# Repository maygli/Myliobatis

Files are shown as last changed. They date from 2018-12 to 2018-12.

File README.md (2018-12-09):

# Myliobatis
FDM 3D printer motherbords based on STM32F407VG/STM32F103RE
This projects contains design of motherbords for FDM 3d printers. Where 3 variants of its:
1) <b>Mobula Ray</b>. This motherbords based on STM32F407VG microcontroller. Motherbords contains:
  - 6 stepper motors drivers TMC2224 (same as TMC2208) controlled by UART. Microsteps, stepper are current controlled by firmware. 
  - 6 PWM output - Heatbed, 3 x heaters, 2 controlled fans
  - 4 temperature inputs
  - 6 inputs for XMIN, XMAX, YMIN, YMAX, ZMIN, ZMAX
  - 3 inputs for filament detectors
  - BlTouch connector
  - onboard WiFi
  - connector for external GSM module
  - connectors SPI/I2C/UART interfaces
  - EXT1/EXT2 connectrs for displays/external SD card
  - SWD connector
  - USB-B
  - micro SD
  - switch after end of print output
  - connectors for 9 programmable pins 
  - board size 150 x 120 mm
  <br>Project page on easyeda.com https://easyeda.com/mmaygli/mid-bro
  2) <b>Manta Ray</b>. This motherbords based on STM32F407VG microcontroller. Has two variants. Variant A has common power suplay for heaters/fans and drivers. 
  Variant B has separate connectors for heaters and motor drivers. Motherbords contains:
  - Connectrs for 6 stepper motors compatible with A4988 (A4988, DRV8825, TMC2100, TMC2130, TMC2208, etc). 
  - 6 PWM output - Heatbed, 3 x heaters, 2 controlled fans
  - 4 temperature inputs
  - 6 inputs for XMIN, XMAX, YMIN, YMAX, ZMIN, ZMAX
  - 3 inputs for filament detectors
  - BlTouch connector
  - onboard WiFi
  - connector for external GSM module
  - connectors SPI/I2C/UART interfaces
  - EXT1/EXT2 connectrs for displays/external SD card
  - SWD connector
  - USB-B
  - micro SD
  - switch after end of print output
  - connectors for 13 programmable pins
  - board size 150 x 120 mm
  <br>Project pages on easyeda.com: https://easyeda.com/mmaygli/test3d, https://easyeda.com/mmaygli/bigbro-external-drivers-common-power
  1) <b>Sting Ray</b>. This motherbords based on STM32F103RE microcontroller.  
  Variant B has separate connectors for heaters and motor drivers. Motherbords contains:
  - Connectrs for 5 stepper motors compatible with A4988 (A4988, DRV8825, TMC2100, TMC2130, TMC2208, etc). 
  - 4 PWM output - Heatbed, 2 x heaters, 1 controlled fans
  - 3 temperature inputs
  - 6 inputs for XMIN, XMAX, YMIN, YMAX, ZMIN, ZMAX
  - filament detector input
  - BlTouch connector (shared with ZMAX, YMAX)
  - connectors I2C/UART interfaces
  - EXT1/EXT2 connectrs for displays/external SD card
  - SWD connector
  - USB-B
  - micro SD
  - board size 112 x 100 mm
<br>Project page on easyeda.com https://easyeda.com/mmaygli/stm32f103-3d-printer-board
<br> Status on 9 of Dec 2018: <b>Boards just designed. Its have never be assembled and tested</b>

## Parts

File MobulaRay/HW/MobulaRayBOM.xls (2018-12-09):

ID | Name | Designator | Footprint | Quantity | Manufacturer Part
1 | TC4427AEOA713 | U1,U7,U8 | SOIC-8_150MIL | 3 | TC4427AEOA713
2 | Hotbead | LED1 | LED-0805 | 1 | 17-21/GHC-YR1S2/3T
3 | Extruder1 | LED2 | LED-0805 | 1 | 17-21/GHC-YR1S2/3T
4 | KF301-2P | EXTRUDER1,EXTRUDER2,EXTRUDER3 | KF301-2P | 3 | ?
5 | KF129-5.08 | HEATBED,POWER | KF129-5.08 | 2 | KF129-5.08
6 | 10 | R20,R7,R8,R18,R37,R13 | 0603' | 6 | 0603WAF1002T5E
7 | 100K | R4,R9,R10,R19,R38,R14 | 0603' | 6 | 0603WAF1002T5E
8 | 3.3K | R5,R6,R11,R24,R21,R36,R12 | 0603' | 7 | 0603WAF1002T5E
9 | IRL3803S | Q5,Q2,Q3,Q7,Q4,Q1 | TO-263-2-COLD | 6 | IRL3803S
10 | Extruder2 | LED3 | LED-0805 | 1 | 17-21/GHC-YR1S2/3T
11 | XH-2A black RHOS | FAN1,TBED1,TEXTR1,TEXTR2,FAN3,+5V,+3.3V,FAN2,TEXTR3 | XH-2A | 9 | XH-2A black RHOS
12 | 22 | R22,R15 | 0603' | 2 | 0603WAF1002T5E
13 | 1.5K | R25 | 0603' | 1 | 0603WAF1002T5E
14 | USB-B-Female-TH_C46393 | USB1 | USB-M-49 | 1 | USB-B-Female-90-TH
15 | Micro SD Card Holder; | J1 | MICRO-SD9+4P-SMD-16.1X14.5X1.85MM | 1 | ?
16 | 47K | R23,R26,R30,R31,R32 | 0603' | 5 | 0603WAF1002T5E
17 | LM2596R-5.0 | U9 | TO-263-5-COLD | 1 | LM2596R-5.0
18 | 100nF | C19,C28,C32,C33,C26,C30,C25,C39,C52,C53,C54,C55,C56,C57 | C0603 | 14 | CC0603KRX7R9BB104
19 | AMS1117-3.3 | U10 | SOT-223 | 1 | AMS1117-3.3
20 | 220uF | C31 | CAP-D6.3XH5.5 | 1 | UT1A221M0605VG
21 | 470uF | C34 | CAP-D12.5XH13.5 | 1 | RVT1V681M1213
22 | SS54 | D1 | SMB(DO-214AA) | 1 | SS54
23 | Power | LED5 | LED-0805 | 1 | 17-21/GHC-YR1S2/3T
24 | 100uF | C27 | CAP-D6.3XH5.5 | 1 | MV101M6R3E055A
25 | 10 uF | C20 | 0603' | 1 | 0603F105M160NT
26 | 10KΩ | R16,R17,R41,R33 | 0603' | 4 | 0603WAF1002T5E
27 | 1N4148W | D2 | SOD-123 | 1 | 1N4148W
28 | 49S8M | Y1 | HC49US | 1 | 49S8M
29 | 22pF | C21,C22 | C0603 | 2 | CC0603JRNPO9BN150
30 | 100uH | L1 | AXIAL-0.5 | 1 | LGA0410-102KP52E
31 | PADI | U25 | PADI(RTL8710) | 1 | pine64
32 | XH-3A | XMIN,YMIN,ZMIN,XMAX,YMAX,ZMAX,FILAMENT1,FILAMENT2,POWER_CONTROL,FILAMENT3 | XH-3A | 10 | XH-3A
33 | 3KΩ | R28,R34,R35,R29 | 0603' | 4 | RK73B1JTTD302J
34 | 10uF | C9,C18,C41,C23 | 0603' | 4 | CL10A106MO8NQNC
35 | FAN2 | LED6 | LED-0805 | 1 | 17-21/GHC-YR1S2/3T
36 | Header-Male-2.54_1x4 | I2C,UART,GSM,SPI | 210S-1X4P | 4 | 210S-1*4P L=11.6MMGold-plated black
37 | Header-Male-2.54_1x2 | BLTOUCH2,H2,H3,H5 | HDR-2X1/2.54 | 4 | 826629-2
38 | Header-Male-2.54_1x3 | BLTOUCH1 | HDR-3X1/2.54 | 1 | Header2.54mm 1*3P
39 | 4.7K | R39,R40 | 0603' | 2 | 0603WAF1002T5E
40 | Header-Male-2.54_1x5 | H1,H4 | DIP-1X5P-2.54MM-M | 2 | 210S-1*5P L=11.6MMGold-plated black
41 | IDC Box 2.0mm 2X5P | EXT2,EXT1 | HDR-IDC-2.0-2X5P | 2 | IDC Box 2.0mm 2X5P
42 | BC847A | Q8 | SOT23-3 | 1 | ?
43 | 47uH | L5 | SMD-10.0X10.0-10A50 | 1 | ABG10A50M470
44 | 7812T | U11 | TO220H | 1 | ?
45 | 100nF | C10,C16,C1,C2,C3,C7,C8,C35,C42,C43,C45,C49,C50,C59,C63,C64,C66,C70,C71,C73 | C0603 | 20 | 0603B104K500NT
46 | 100uF | C11,C29,C17,C24,C44,C58,C65,C72 | CAP-D6.3XH7.7 | 8 | UT1V101M0607VG
47 | LED | LED8 | LED-0805 | 1 | 17-21/GHC-YR1S2/3T
48 | FAN1 | LED4 | LED-0805 | 1 | 17-21/GHC-YR1S2/3T
49 | 1N4007 | D4 | 1N4007_SURFACE_MOUNT_M1_THRU_M7 | 1 | ?
50 | S3MB | D3 | SMB(DO-214AA) | 1 | S3MB
51 | BOOT0 | CN1 | H3-2.54 | 1 | ?
52 | Reset | SW3 | KEY-6.0*6.0 | 1 | Switch,6*6*5Plastic head,260G, 0.25mm,DIP2
53 | 74HC4051PW,118 | U14 | TSSOP-16 | 1 | 74HC4051PW,118
54 | TMC2224 | U2,U3,U4,U5,U6,U12 | QFN28G_0.5-5X5MM | 6 | TMC2224
55 | XH-4AK M | E3,E2,E1,X,Y,Z,Z1,Z2 | XH-4A | 8 | -
56 | 22nF | C4,C6,C37,C40,C46,C48,C60,C62,C67,C69,C74,C76 | C0603 | 12 | 0603B104K500NT
57 | 2.2uF | C5,C38,C47,C61,C68,C75 | C0603 | 6 | 0603B104K500NT
58 | 0.1Ω | R1,R2,R3,R42,R43,R44,R45,R46,R47,R48,R49,R50 | 2512 | 12 | 2512W4F100LT5E
59 | Header-Male-2.54_1x4 | EXT3_DRV,EXT2_DRV,X_DRV,Y_DRV,Z_DRV,EXT1_DRV | DIP-1X4P-2.54MM-M | 6 | 210S-1*4P L=11.6MMGold-plated black
60 | STM32F407VGT6 | U13 | LQFP-100_14X14X05P | 1 | STM32F407VGT6

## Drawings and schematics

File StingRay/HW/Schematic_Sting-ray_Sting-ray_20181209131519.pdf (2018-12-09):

# Vmot 16 Motor Connection

+5V

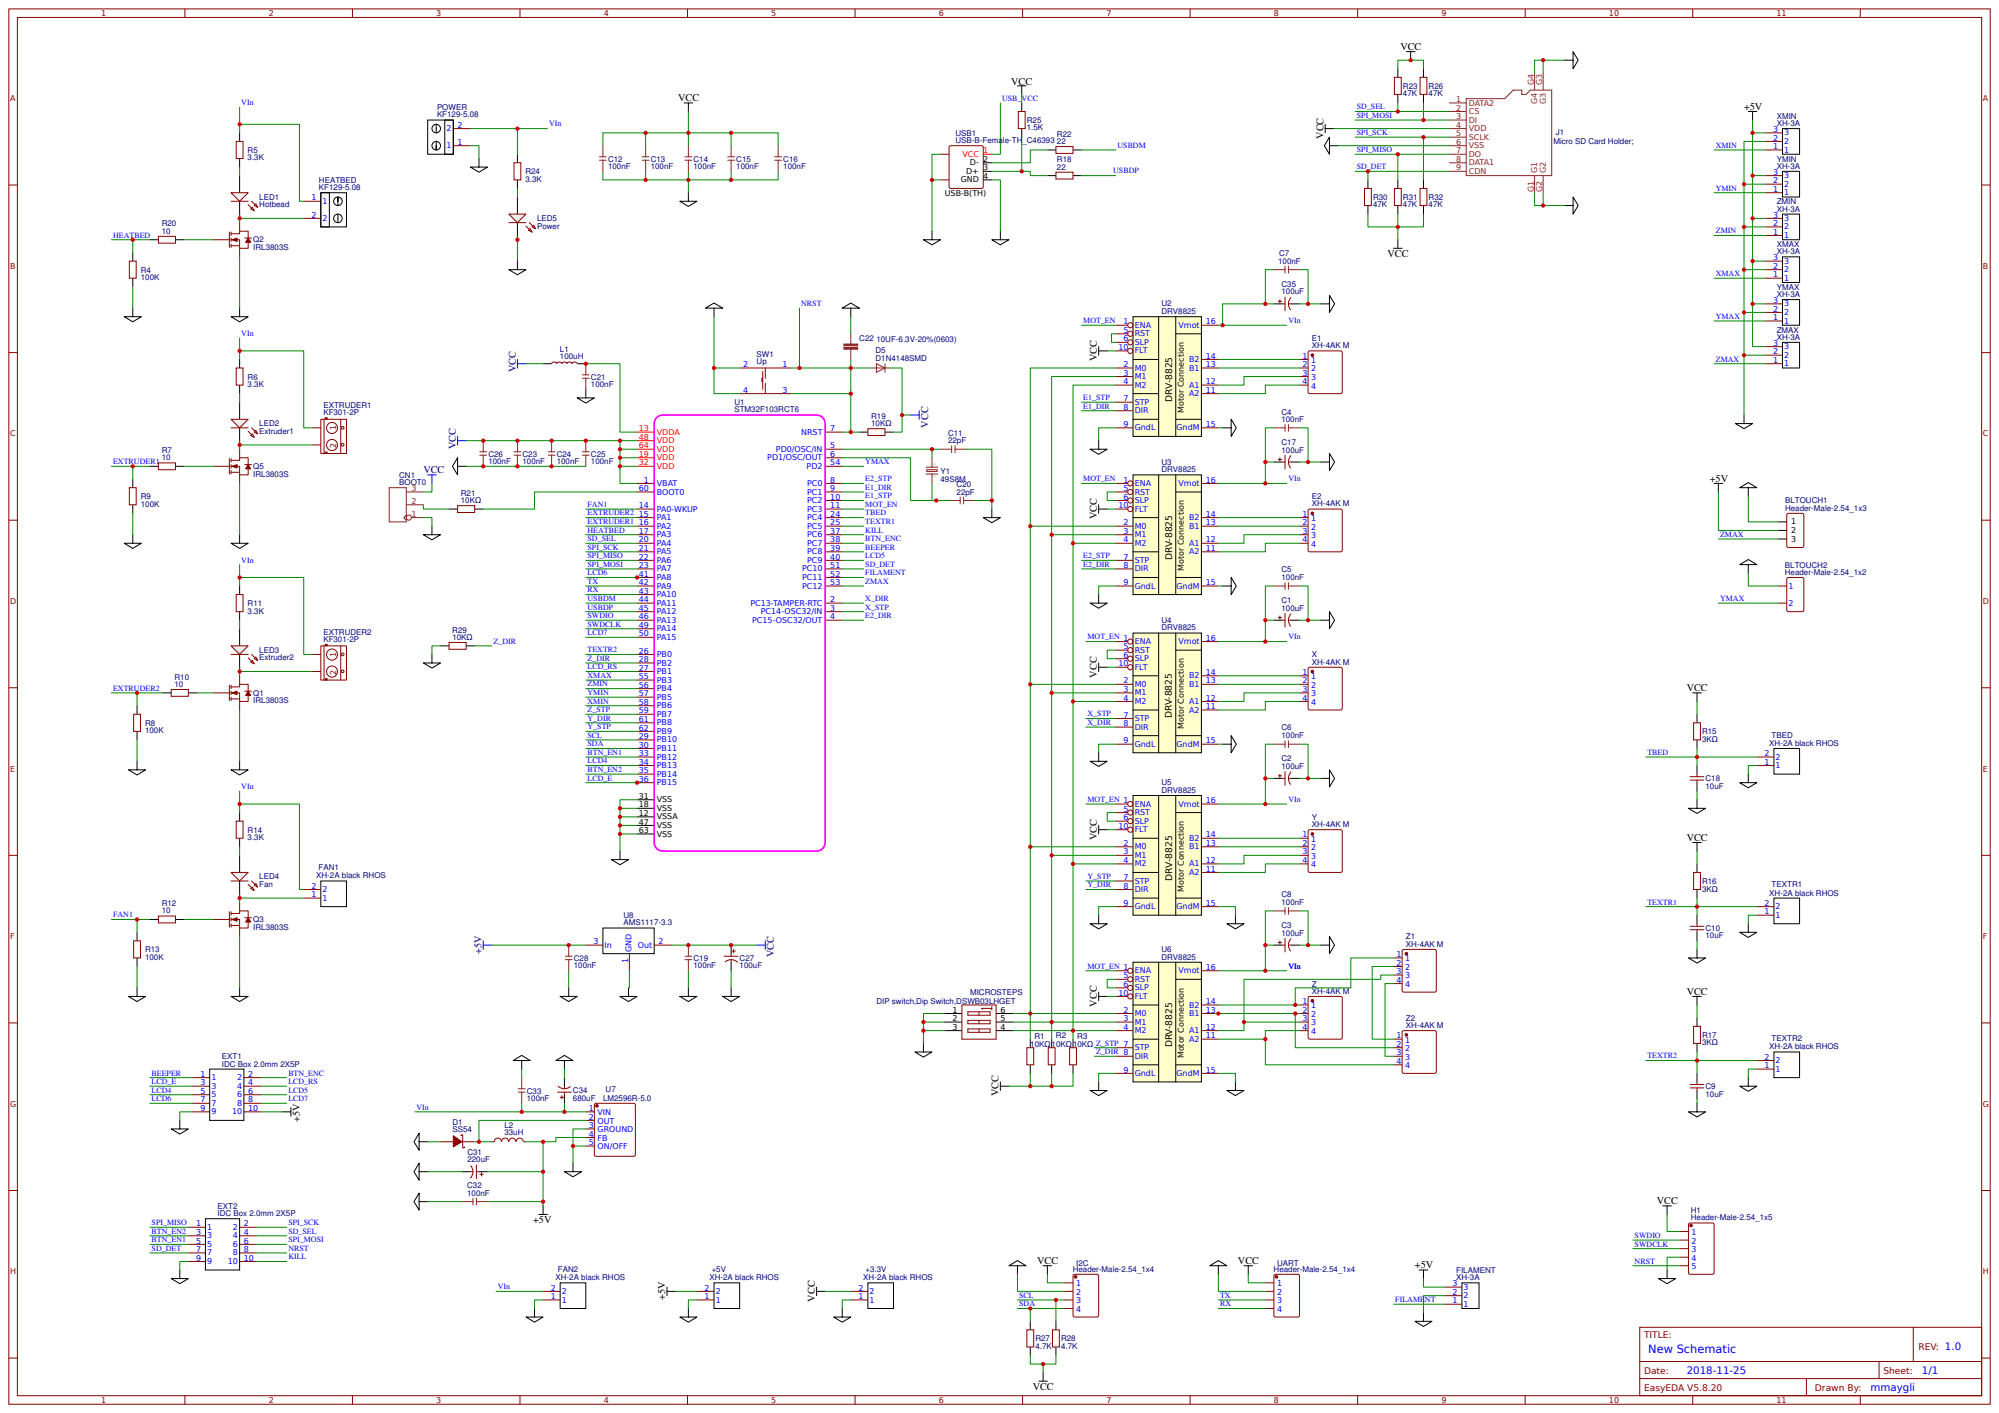
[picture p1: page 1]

Micro SD Card Holder;

DIP switch,Dip Switch,DSWB03LHGET

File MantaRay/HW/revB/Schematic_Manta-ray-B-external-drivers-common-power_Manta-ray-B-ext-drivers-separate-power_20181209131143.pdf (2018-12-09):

### VCC

### VCC

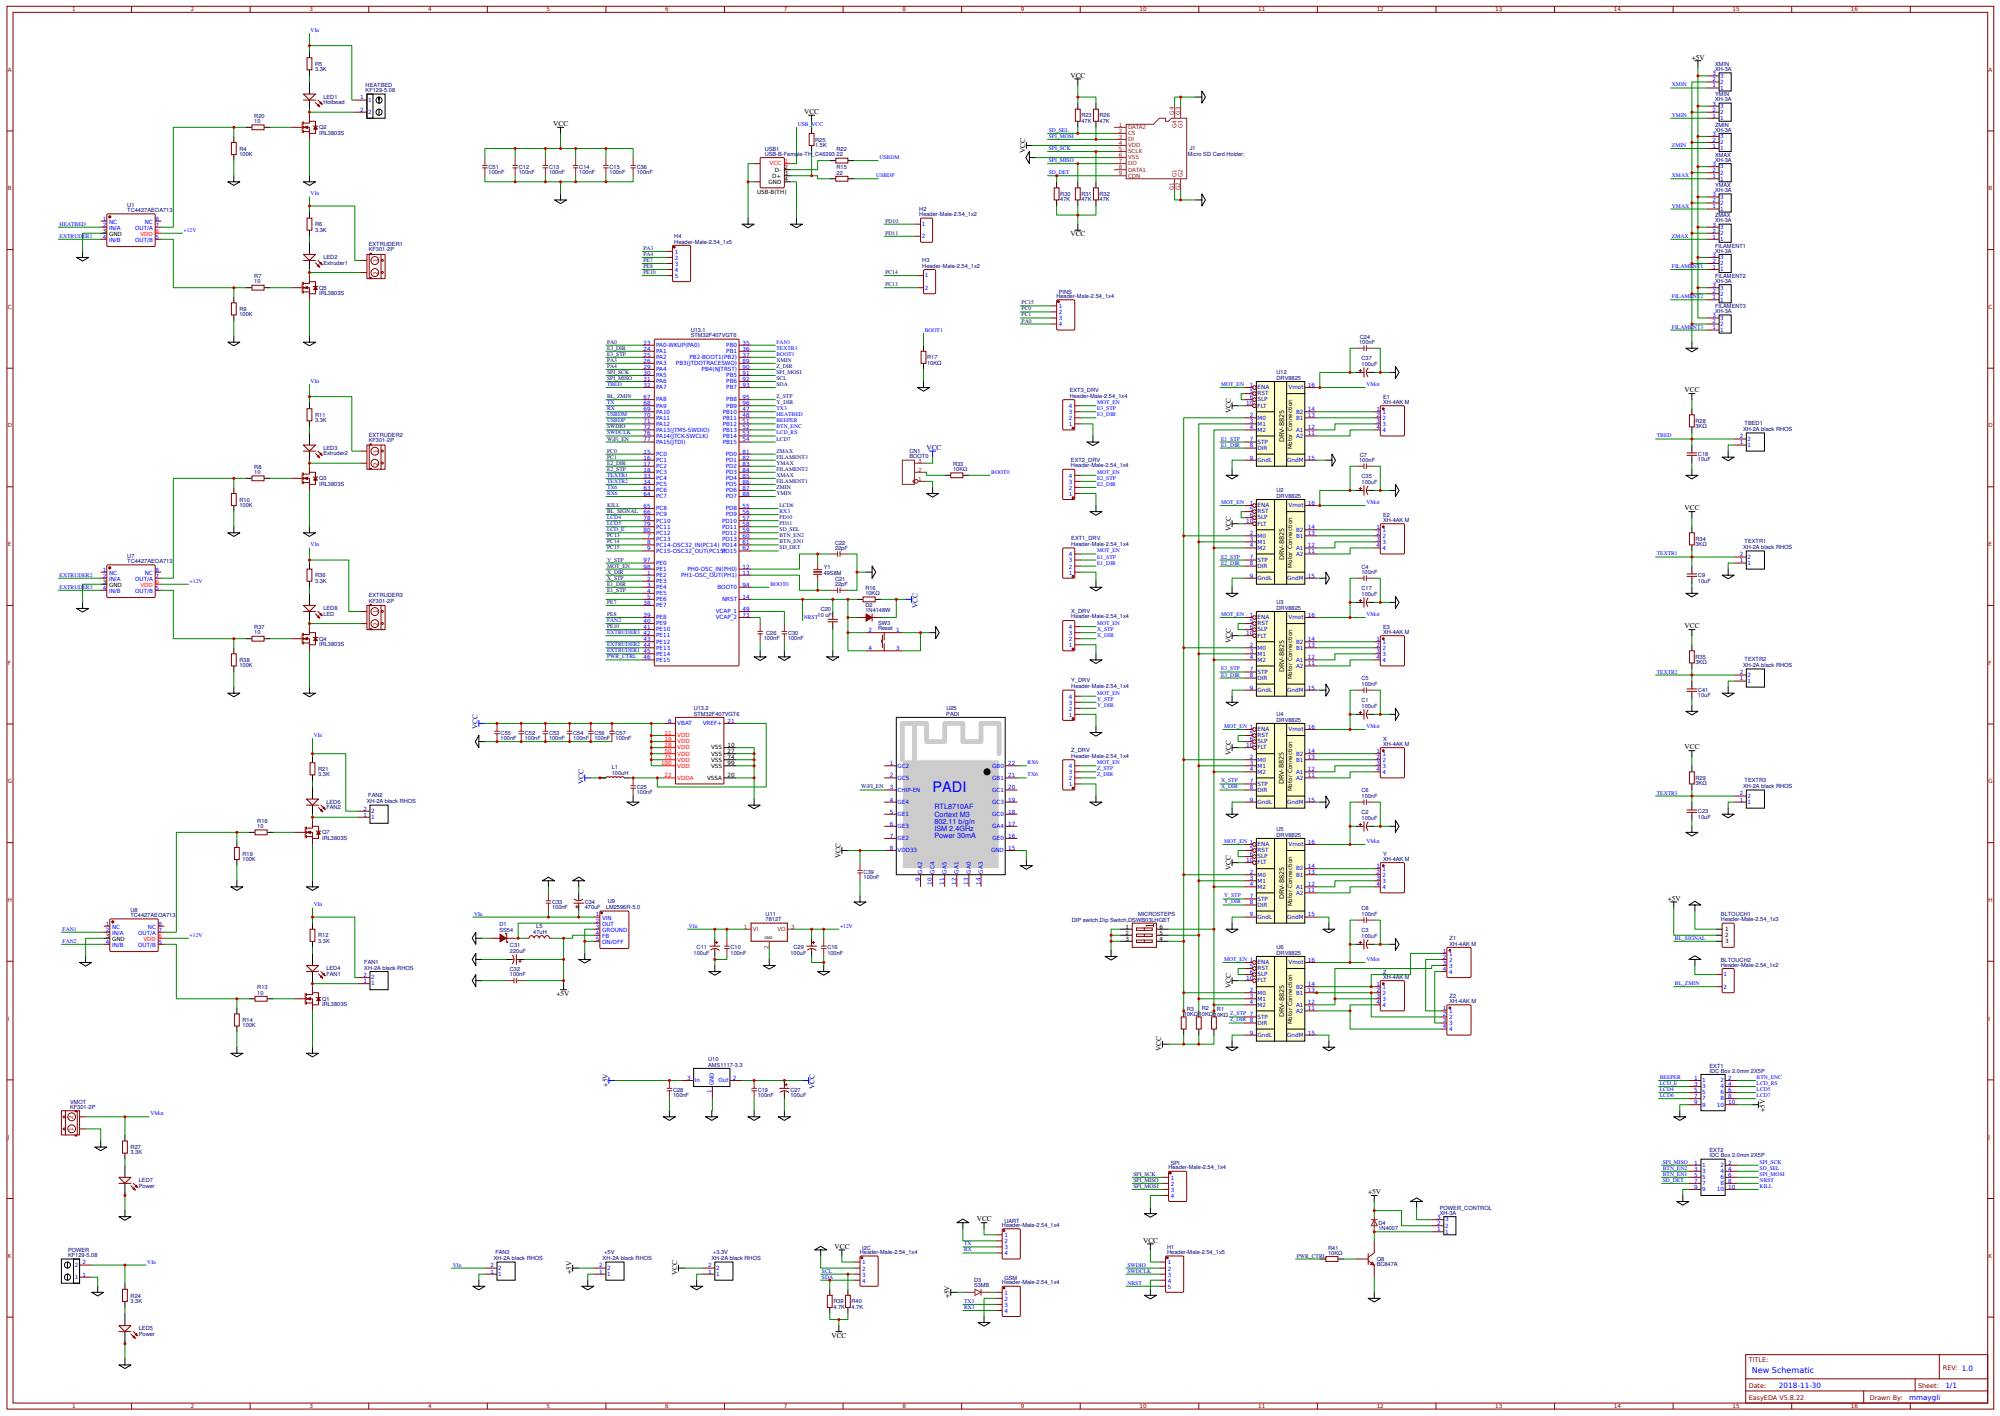
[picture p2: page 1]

Micro SD Card Holder;

DIP switch,Dip Switch,DSWB03LHGET

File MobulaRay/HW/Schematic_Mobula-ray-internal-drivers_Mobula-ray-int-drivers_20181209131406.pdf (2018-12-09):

### VCC

### VCC

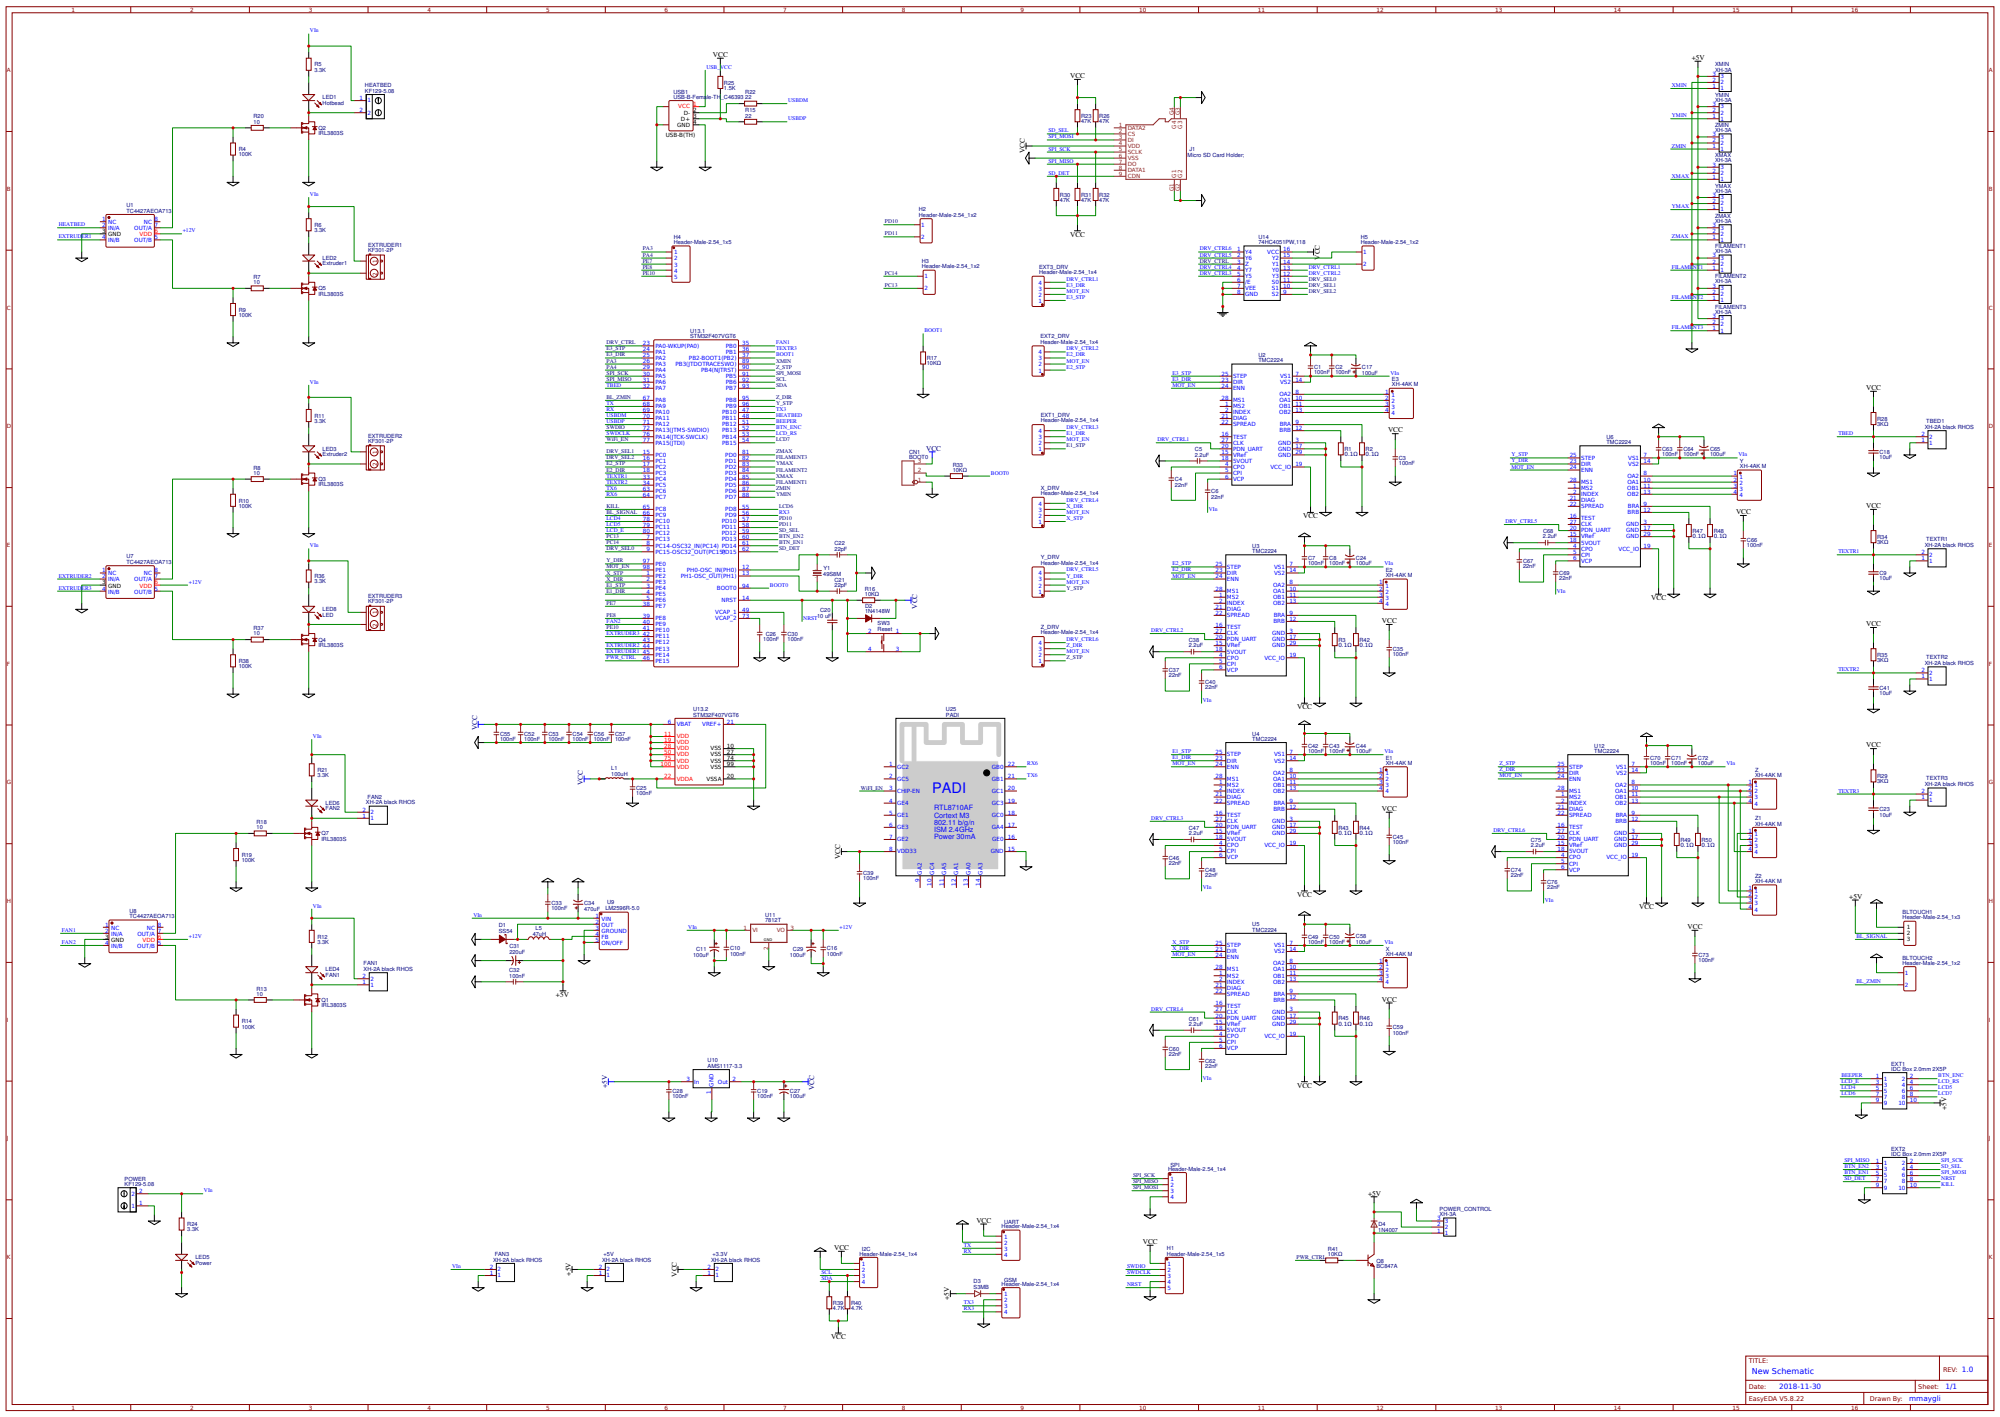
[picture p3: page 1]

Micro SD Card Holder;

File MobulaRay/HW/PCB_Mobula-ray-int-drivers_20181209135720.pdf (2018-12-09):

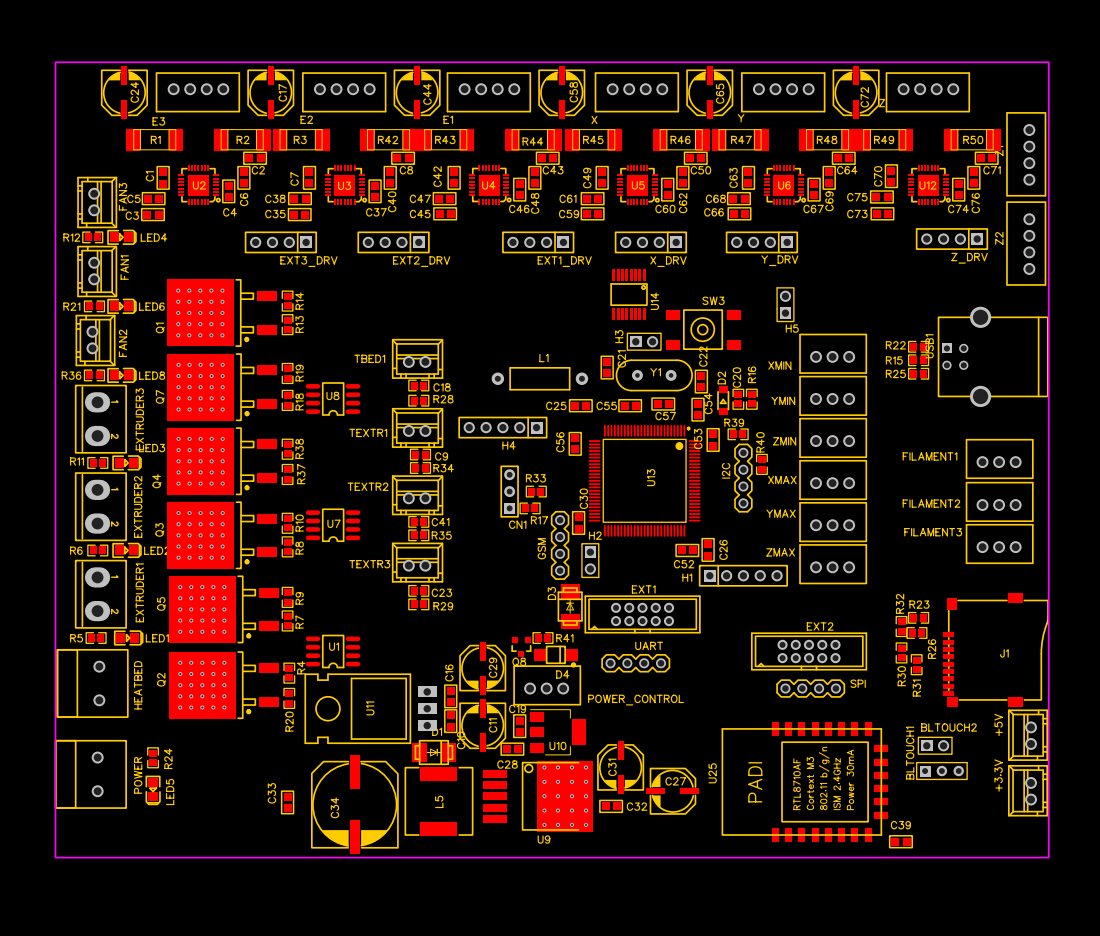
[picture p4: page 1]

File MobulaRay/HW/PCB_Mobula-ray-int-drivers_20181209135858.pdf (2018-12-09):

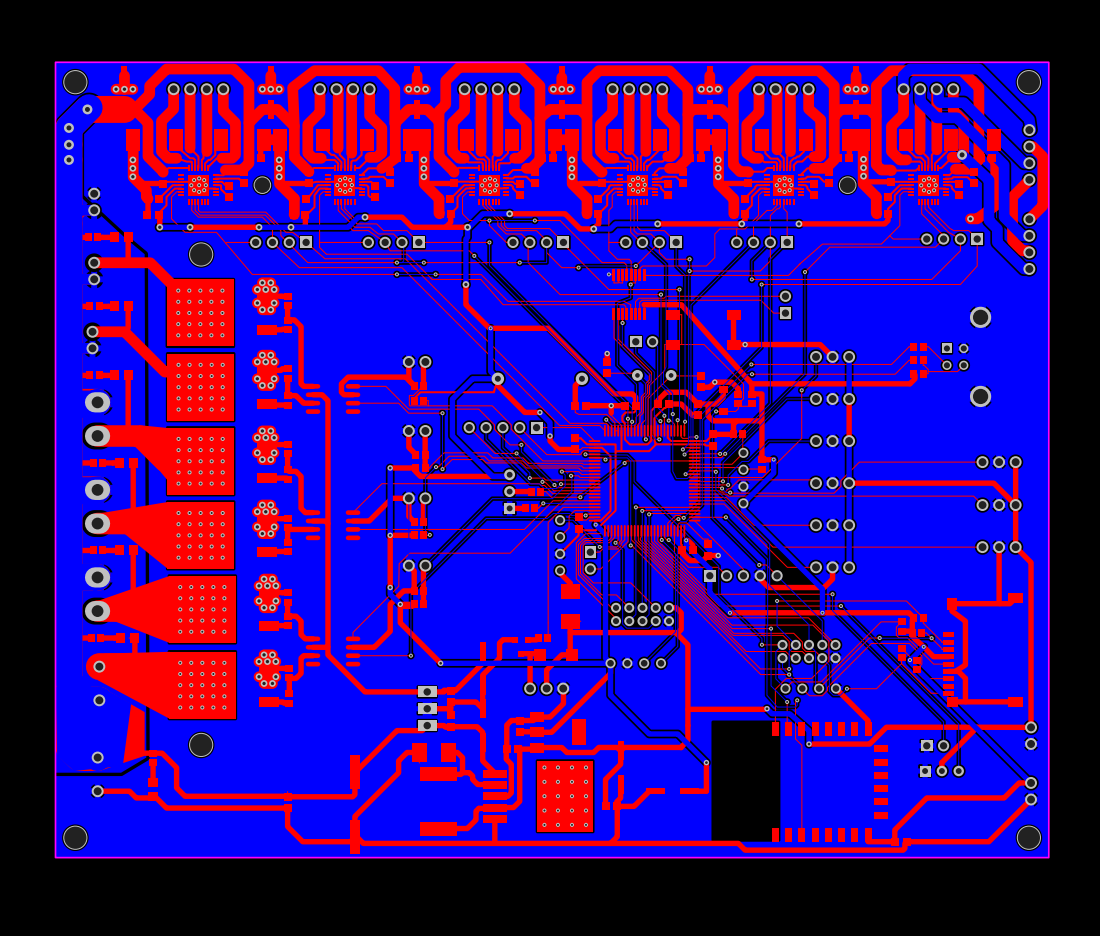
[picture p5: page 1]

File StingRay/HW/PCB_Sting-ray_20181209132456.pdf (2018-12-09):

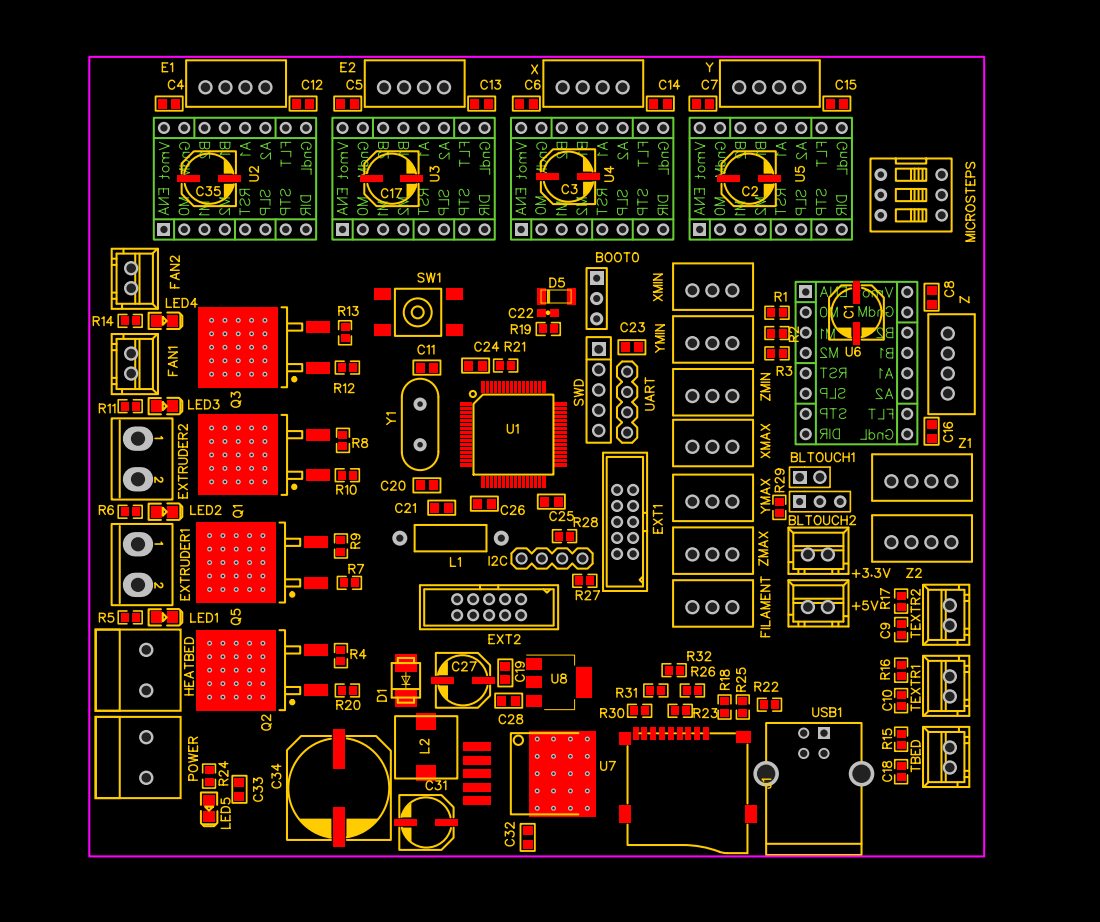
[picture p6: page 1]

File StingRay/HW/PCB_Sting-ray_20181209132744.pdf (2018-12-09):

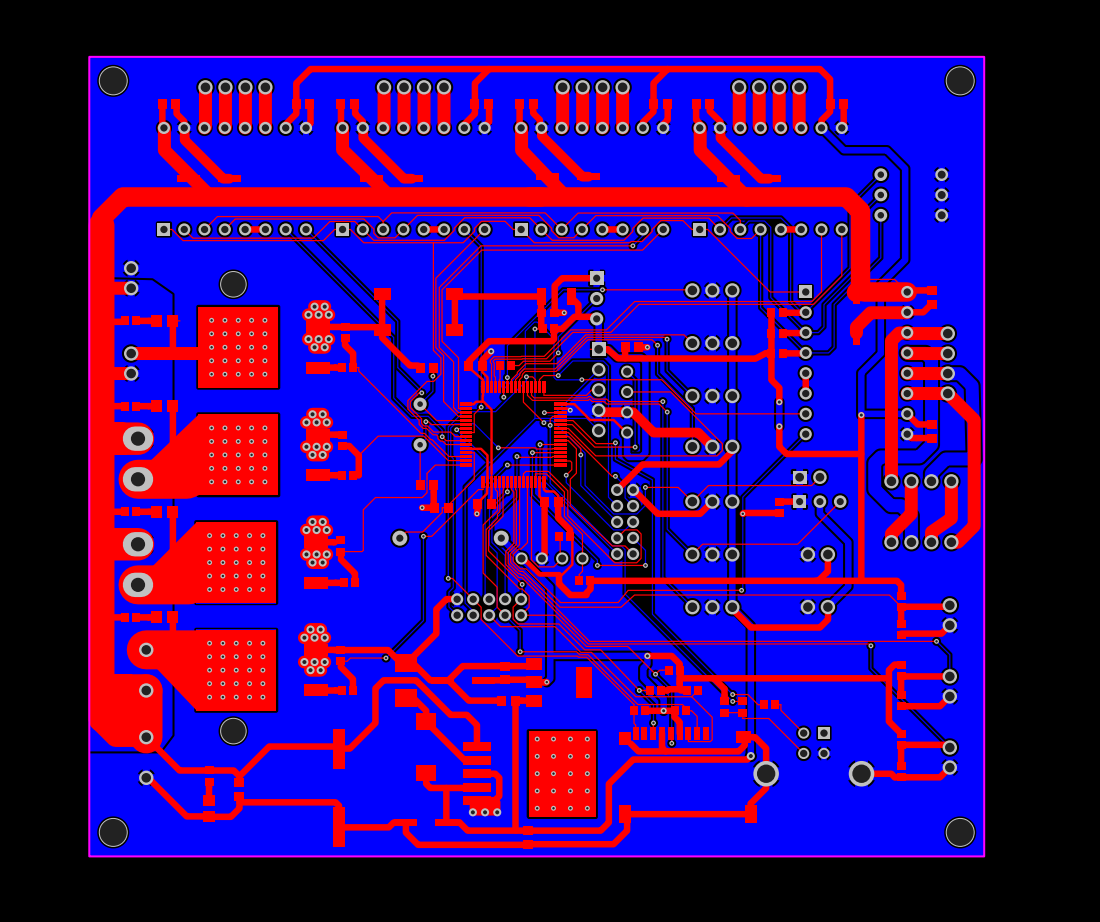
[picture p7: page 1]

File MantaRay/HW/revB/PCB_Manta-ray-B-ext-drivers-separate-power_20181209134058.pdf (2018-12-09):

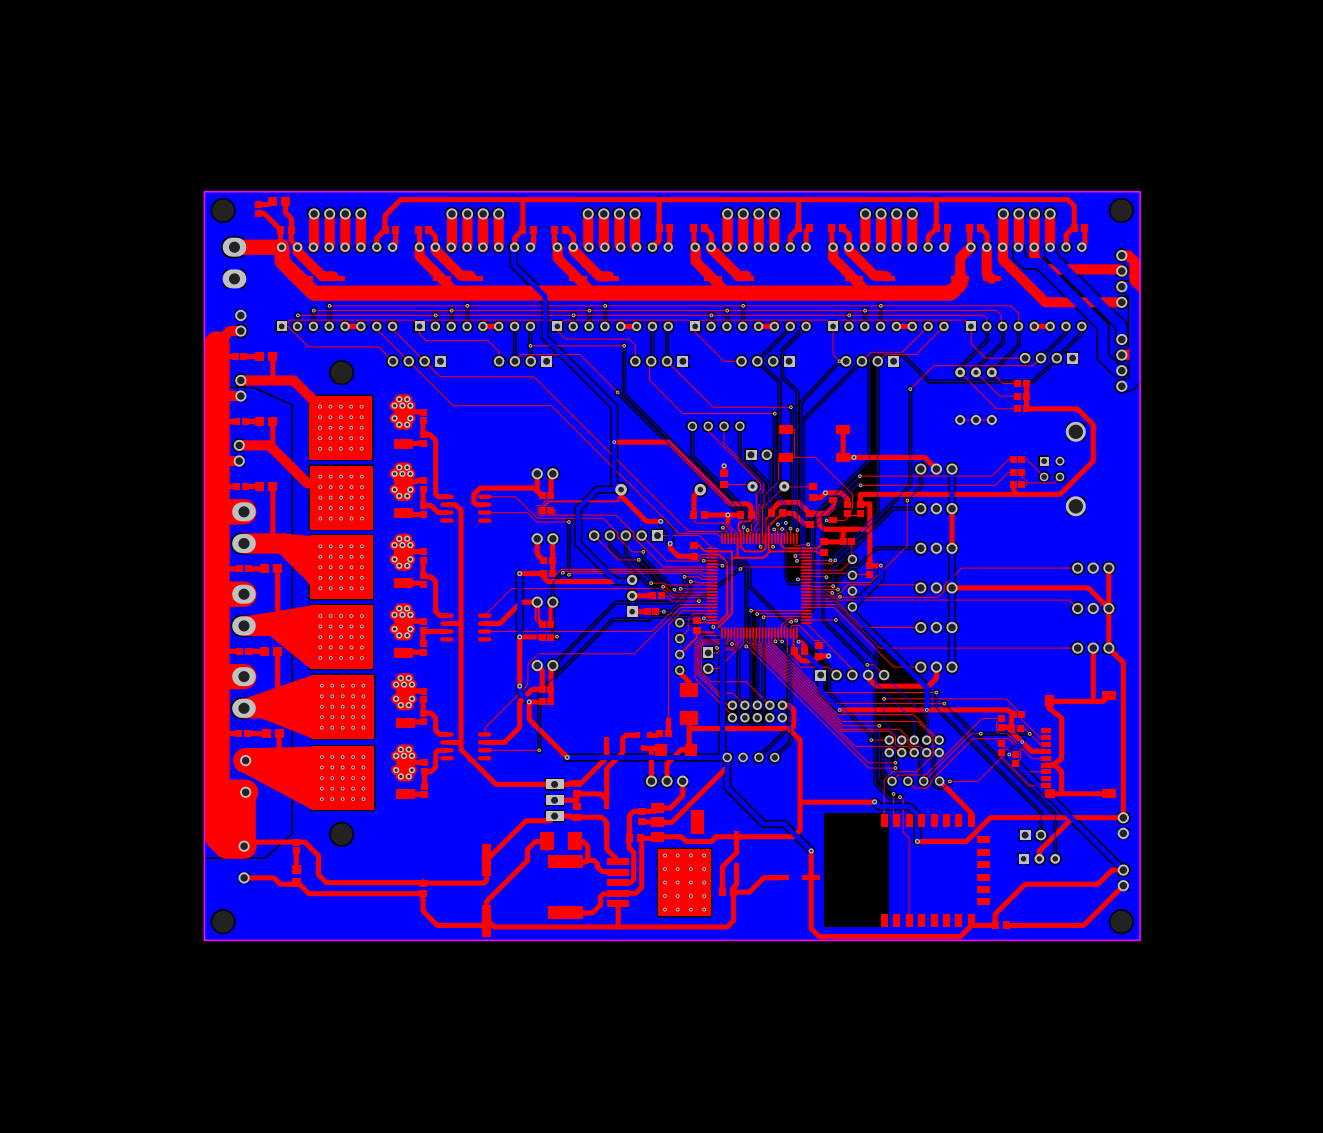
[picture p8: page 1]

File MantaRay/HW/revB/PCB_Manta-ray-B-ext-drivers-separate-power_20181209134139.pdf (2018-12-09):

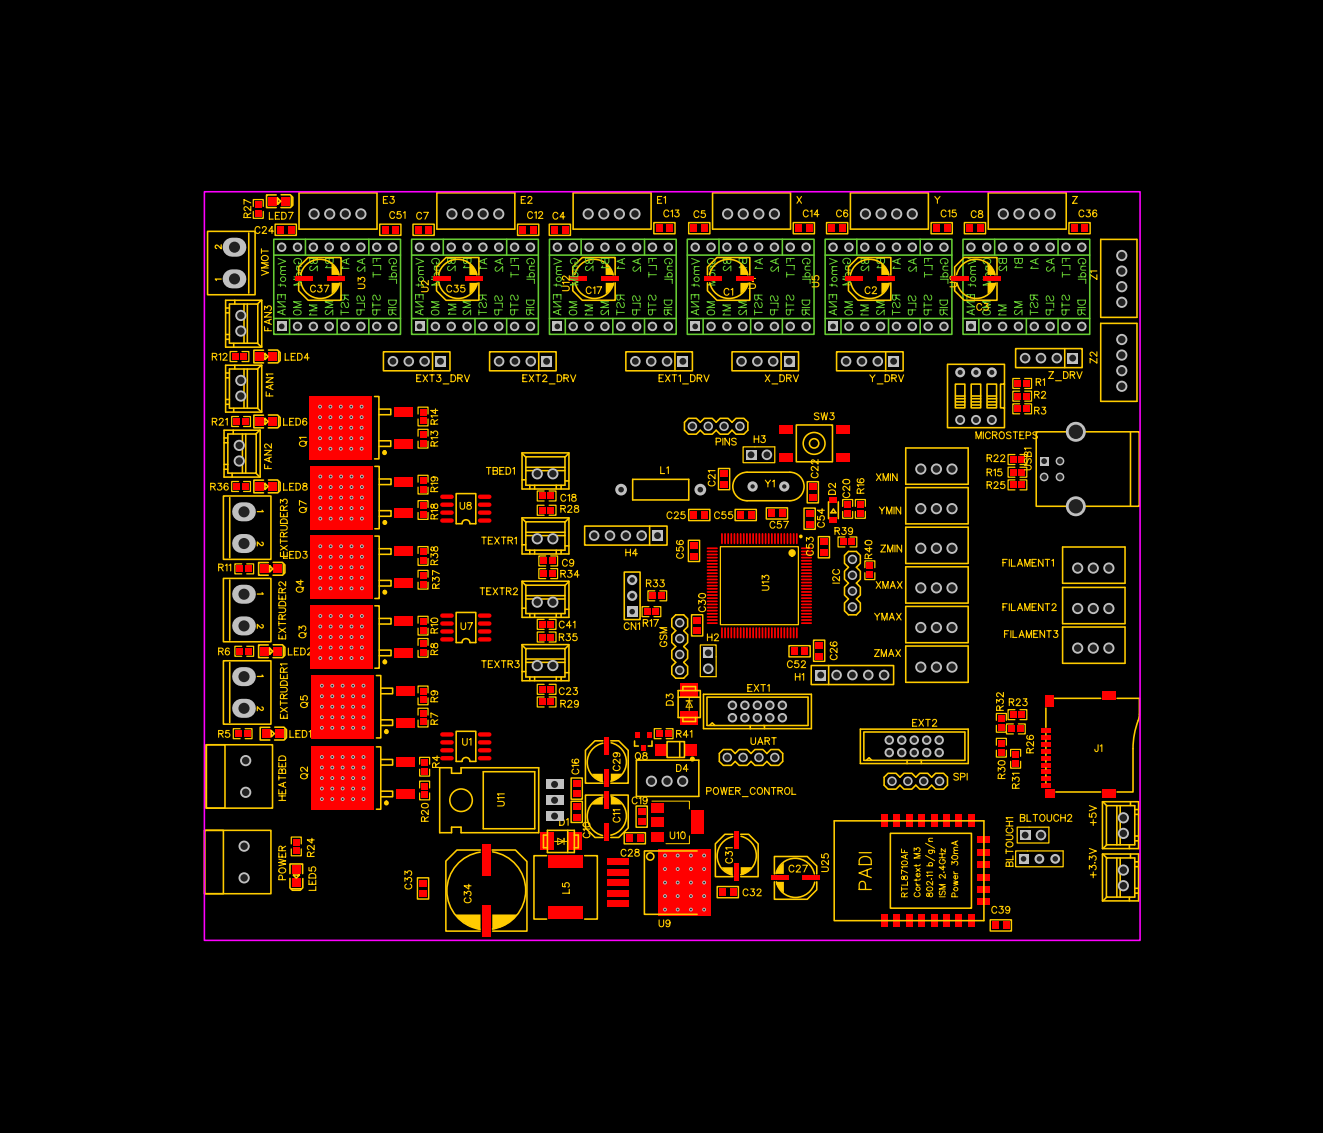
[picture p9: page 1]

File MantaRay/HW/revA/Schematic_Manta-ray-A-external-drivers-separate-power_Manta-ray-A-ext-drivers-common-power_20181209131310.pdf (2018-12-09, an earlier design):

### VCC

### VCC

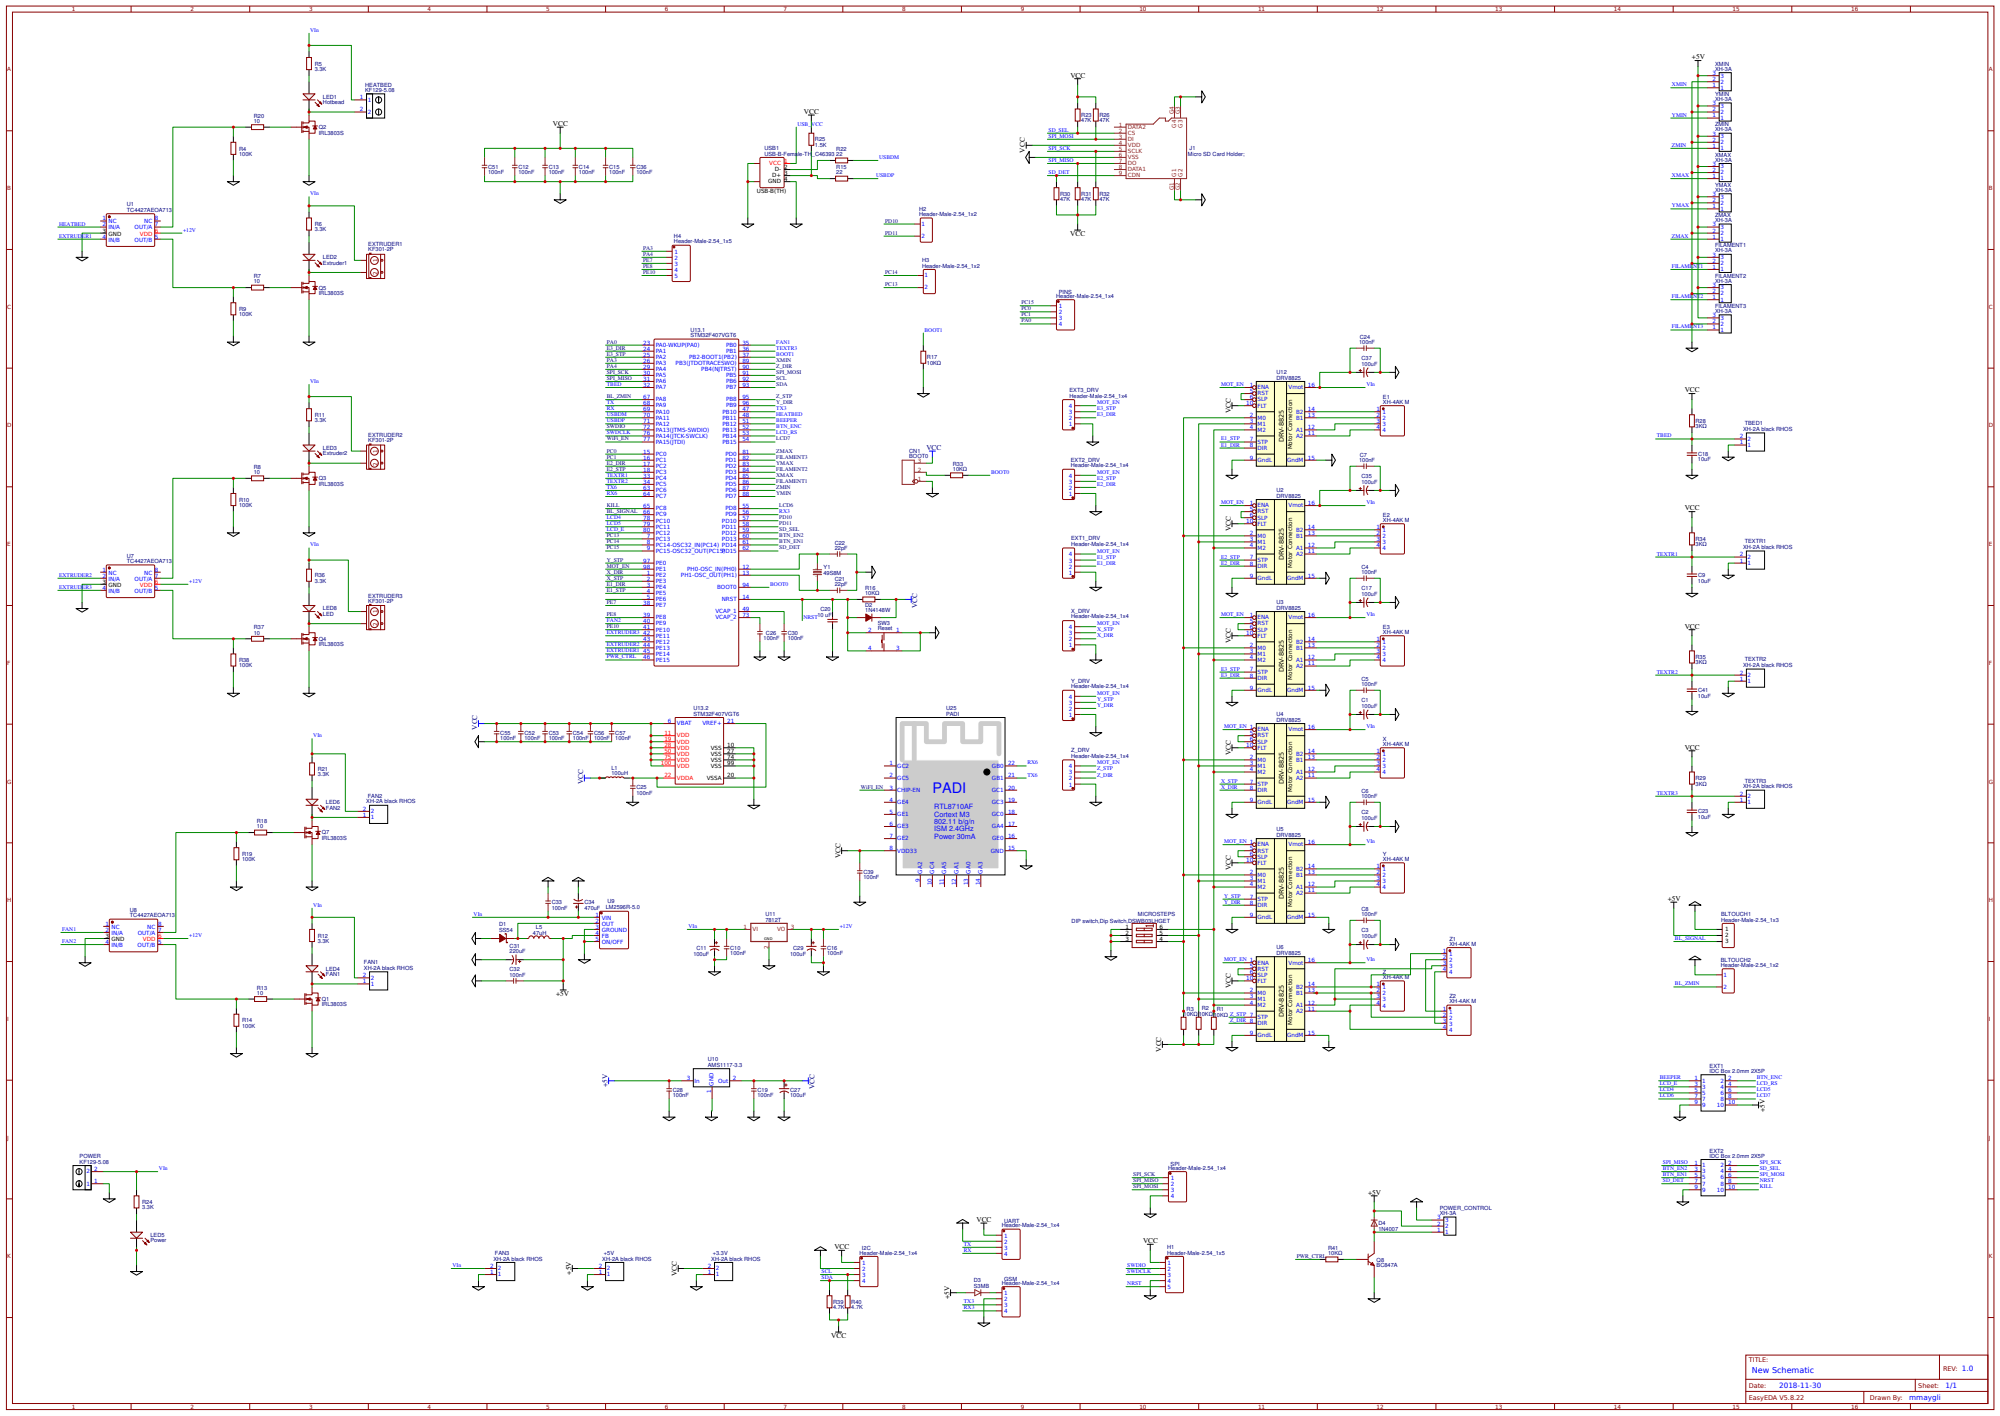
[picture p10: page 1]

Micro SD Card Holder;

DIP switch,Dip Switch,DSWB03LHGET

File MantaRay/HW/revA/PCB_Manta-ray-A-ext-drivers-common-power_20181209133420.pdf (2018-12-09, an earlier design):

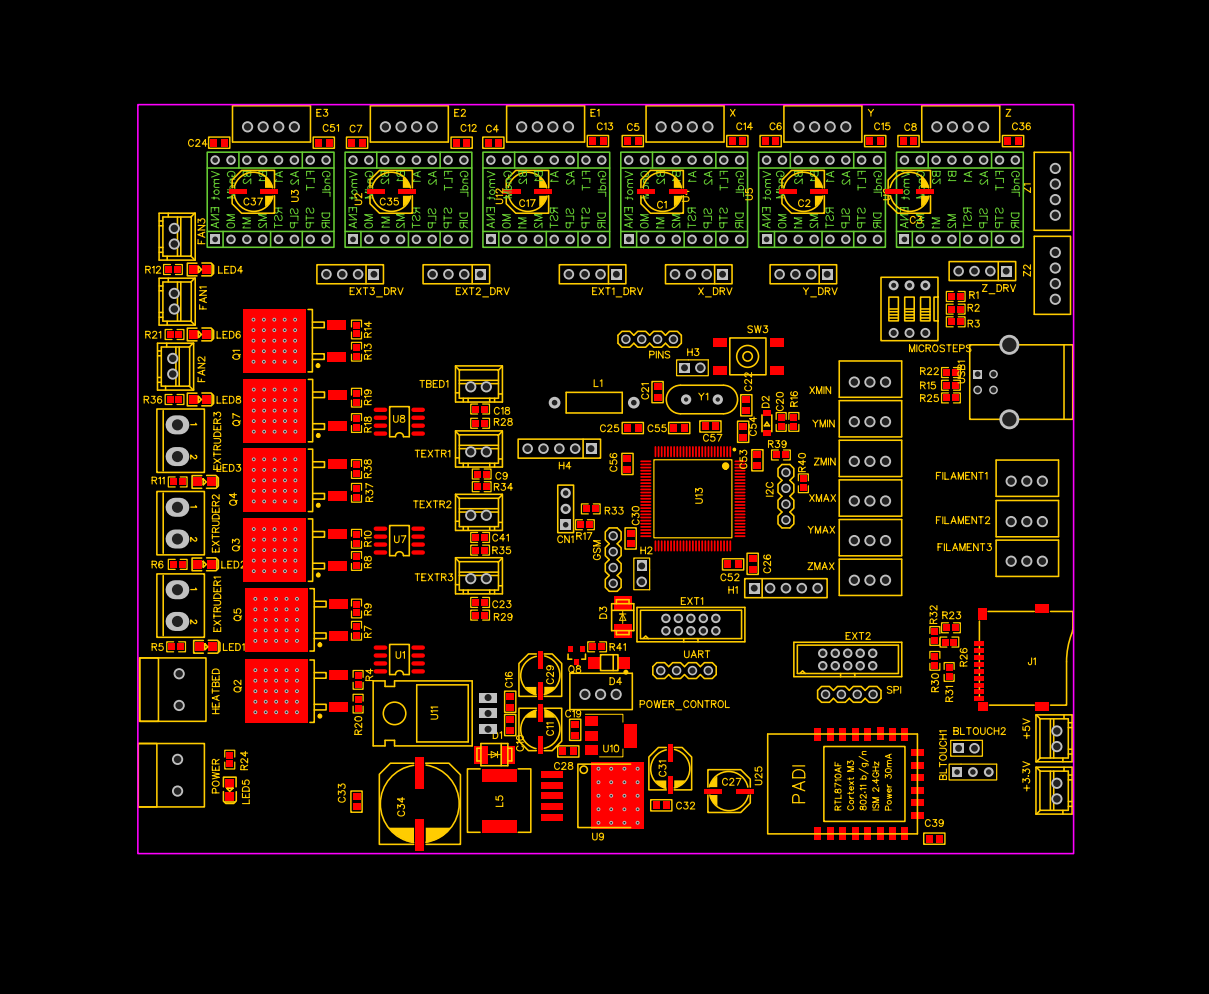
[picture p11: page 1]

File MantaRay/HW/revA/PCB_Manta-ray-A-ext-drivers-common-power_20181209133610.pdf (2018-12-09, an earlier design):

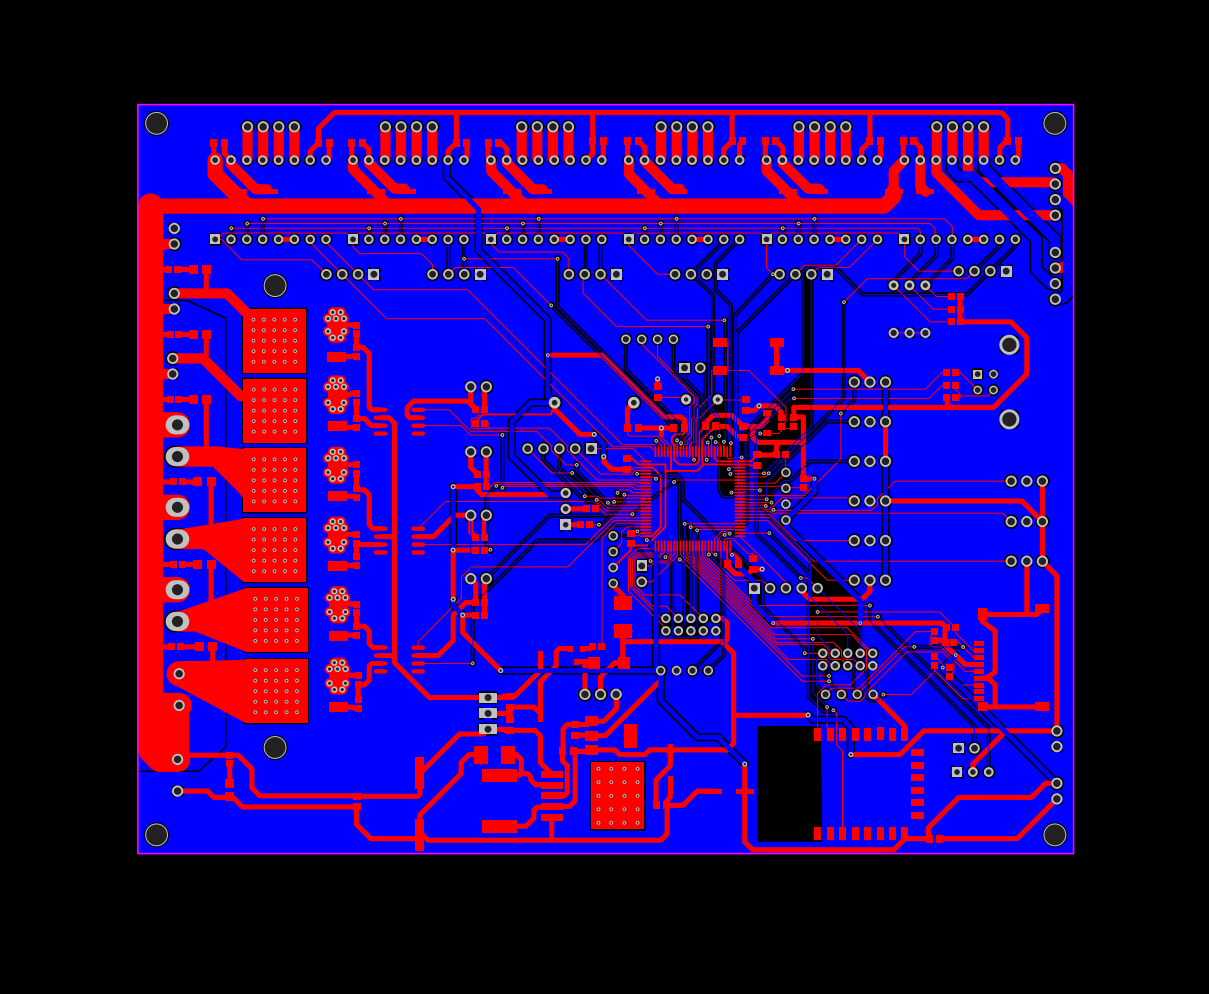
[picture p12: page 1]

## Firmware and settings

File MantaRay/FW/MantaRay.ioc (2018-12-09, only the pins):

Mcu.UserName=STM32F407VGTx
PA0-WKUP.GPIO_Label=UART4(MOTOR_DRV_CONTROL)
PA0-WKUP.Signal=UART4_TX
PA1.GPIO_Label=E3_DIR
PA1.Signal=GPIO_Output
PA10.Signal=USART1_RX
PA11.Signal=USB_OTG_FS_DM
PA12.Signal=USB_OTG_FS_DP
PA13.Signal=SYS_JTMS-SWDIO
PA14.Signal=SYS_JTCK-SWCLK
PA15.GPIO_Label=WiFi_EN
PA15.Signal=GPIO_Input
PA2.GPIO_Label=E3_STP
PA2.Signal=GPIO_Output
PA5.Signal=SPI1_SCK
PA6.Signal=SPI1_MISO
PA7.GPIO_Label=TBED(ADC1/7)
PA7.Signal=ADCx_IN7
PA8.GPIO_Label=BL_ZMIN
PA8.Signal=GPIO_Input
PA9.Signal=USART1_TX
PB0.GPIO_Label=FAN1(TIM3/3)
PB0.Signal=S_TIM3_CH3
PB1.GPIO_Label=TEXTR3(ADC1/9)
PB1.Signal=ADCx_IN9
PB10.GPIO_Label=USART3_TX(GSM)
PB10.Signal=USART3_TX
PB11.GPIO_Label=HEATBED(TIM2/4)
PB11.Signal=S_TIM2_CH4
PB12.GPIO_Label=BEEPER
PB12.Signal=GPIO_Output
PB13.GPIO_Label=BTN_ENC
PB13.Signal=GPIO_Output
PB14.GPIO_Label=LCD_RS
PB14.Signal=GPIO_Output
PB15.GPIO_Label=LCD7
PB15.Signal=GPIO_Output
PB3.GPIO_Label=XMIN
PB3.Signal=GPIO_Input
PB4.GPIO_Label=Z_DIR
PB4.Signal=GPIO_Output
PB5.Signal=SPI1_MOSI
PB6.Signal=I2C1_SCL
PB7.Signal=I2C1_SDA
PB8.GPIO_Label=Z_STP
PB8.Signal=GPIO_Output
PB9.GPIO_Label=Y_DIR
PB9.Signal=GPIO_Output
PC0.GPIO_Label=DRV_SEL1
PC0.Signal=GPIO_Output
PC1.GPIO_Label=DRV_SEL2
PC1.Signal=GPIO_Output
PC10.GPIO_Label=SPI3_SCK(LCD4)
PC10.Signal=SPI3_SCK
PC11.GPIO_Label=SPI3_MISO(LCD5)
PC11.Signal=SPI3_MISO
PC12.GPIO_Label=SPI3_MOSI(LCD_E)
PC12.Signal=SPI3_MOSI
PC15-OSC32_OUT.GPIO_Label=DRV_SEL0
PC15-OSC32_OUT.Signal=GPIO_Output
PC2.GPIO_Label=E2_DIR
PC2.Signal=GPIO_Output
PC3.GPIO_Label=E2_STP
PC3.Signal=GPIO_Output
PC4.GPIO_Label=TEXTR1(ADC1/14)
PC4.Signal=ADCx_IN14
PC5.GPIO_Label=TEXTR2(ADC1/15)
PC5.Signal=ADCx_IN15
PC6.GPIO_Label=USART6_TX(WiFi)
PC6.Signal=USART6_TX
PC7.GPIO_Label=USART6_RX(WiFi)
PC7.Signal=USART6_RX
PC8.GPIO_Label=KILL
PC8.Signal=GPIO_Input
PC9.GPIO_Label=BL_SIGNAL
PC9.Signal=GPIO_Output
PD0.GPIO_Label=ZMAX
PD0.Signal=GPIO_Input
PD1.GPIO_Label=FILAMENT3
PD1.Signal=GPIO_Input
PD12.GPIO_Label=SD_SEL
PD12.Signal=GPIO_Output
PD13.GPIO_Label=BTN_EN2
PD13.Signal=GPIO_Input
PD14.GPIO_Label=BTN_EN1
PD14.Signal=GPIO_Input
PD15.GPIO_Label=SD_DET
PD15.Signal=GPIO_Input
PD2.GPIO_Label=YMAX
PD2.Signal=GPIO_Input
PD3.GPIO_Label=FILAMENT2
PD3.Signal=GPIO_Input
PD4.GPIO_Label=XMAX
PD4.Signal=GPIO_Input
PD5.GPIO_Label=FILAMENT1
PD5.Signal=GPIO_Input
PD6.GPIO_Label=ZMIN
PD6.Signal=GPIO_Input
PD7.GPIO_Label=YMIN
PD7.Signal=GPIO_Input
PD8.GPIO_Label=LCD6
PD8.Signal=GPIO_Output
PD9.GPIO_Label=USART3_RX(GSM)
PD9.Signal=USART3_RX
PE0.GPIO_Label=Y_STP
PE0.Signal=GPIO_Output
PE1.GPIO_Label=MOT_EN
PE1.Signal=GPIO_Output
PE11.GPIO_Label=EXTRUDER3(TIM1/2)
PE11.Signal=S_TIM1_CH2
PE13.GPIO_Label=EXTRUDER2(TIM1/3)
PE13.Signal=S_TIM1_CH3
PE14.GPIO_Label=EXTRUDER1(TIM1/4)
PE14.Signal=S_TIM1_CH4
PE15.GPIO_Label=PWR_CTRL
PE15.Signal=GPIO_Output
PE2.GPIO_Label=X_DIR
PE2.Signal=GPIO_Output
PE3.GPIO_Label=X_STP
PE3.Signal=GPIO_Output
PE4.GPIO_Label=E1_DIR
PE4.Signal=GPIO_Output
PE5.GPIO_Label=E1_STP
PE5.Signal=GPIO_Output
PE9.GPIO_Label=FAN2(TIM1/1)
PE9.Signal=S_TIM1_CH1
PH0-OSC_IN.Signal=RCC_OSC_IN
PH1-OSC_OUT.Signal=RCC_OSC_OUT

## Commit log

2018-12-09 HW designs were added
    [MantaRayABOM.xls, MantaRayBBOM.xls, MobulaRayBOM.xls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]
2019-01-11 Altium files were added to StringRay
    [Stingray.pcbdoc, Stingray.schdoc]
2019-01-14 StingRay Altium files were updated
    [Stingray.pcbdoc, Stingray.schdoc]
